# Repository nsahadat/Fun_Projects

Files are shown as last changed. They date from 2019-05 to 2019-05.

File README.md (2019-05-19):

# Fun_Projects
Hobby hardware/software embedded projects:

#### Door_Lock project is built from scratch to control your own door lock using Mobile App via WiFi:
This project includes the following in 4 folders: 
1. PCB design of the board using KiCAD
2. Firmware development of the WiFi module ESP8266
3. Designing the mechanical 3D printed part in Solidworks
4. Android app is developed using MIT App Inventor

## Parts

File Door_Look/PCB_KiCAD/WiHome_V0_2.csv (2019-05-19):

Reference | Value | OrderLink
U2 | LDO_SPX3819 | https://www.digikey.com/scripts/DkSearch/dksus.dll?Detail&itemSeq=225275258&uq=636276384097700233
J1 | ACin | https://www.digikey.com/scripts/DkSearch/dksus.dll?Detail&itemSeq=225275253&uq=636276384097700233
U5 | ESP-12F | http://www.gearbest.com/transmitters-receivers-module/pp_227650.html
D3 | LED | https://www.digikey.com/scripts/DkSearch/dksus.dll?Detail&itemSeq=225275247&uq=636276384097700233
D2 | LED | https://www.digikey.com/scripts/DkSearch/dksus.dll?Detail&itemSeq=225275247&uq=636276384097700233
R7 | 122 | https://www.digikey.com/scripts/DkSearch/dksus.dll?Detail&itemSeq=225275251&uq=636276384097700233
C1 | 10uF | https://www.digikey.com/scripts/DkSearch/dksus.dll?Detail&itemSeq=225275264&uq=636276384097700233
C8 | 0.1uF | https://www.digikey.com/scripts/DkSearch/dksus.dll?Detail&itemSeq=225275262&uq=636276384097700233
C7 | 1uF | https://www.digikey.com/scripts/DkSearch/dksus.dll?Detail&itemSeq=225275264&uq=636276384097700233
J2 | ACout | https://www.digikey.com/scripts/DkSearch/dksus.dll?Detail&itemSeq=225275253&uq=636276384097700233
J3 | FTDI_CON | https://www.digikey.com/scripts/DkSearch/dksus.dll?Detail&itemSeq=225275250&uq=636276384097700233
Q2 | MMBT3904_BEC | https://www.digikey.com/scripts/DkSearch/dksus.dll?Detail&itemSeq=225275260&uq=636276384097700233
R6 | 1k | https://www.digikey.com/scripts/DkSearch/dksus.dll?Detail&itemSeq=225275249&uq=636276384097700233
R5 | 1k | https://www.digikey.com/scripts/DkSearch/dksus.dll?Detail&itemSeq=225275249&uq=636276384097700233
C2 | 0.1uF | https://www.digikey.com/scripts/DkSearch/dksus.dll?Detail&itemSeq=225275262&uq=636276384097700233
C3 | 1uF | https://www.digikey.com/scripts/DkSearch/dksus.dll?Detail&itemSeq=225275264&uq=636276384097700233
C4 | 0.1uF | https://www.digikey.com/scripts/DkSearch/dksus.dll?Detail&itemSeq=225275262&uq=636276384097700233
D1 | D | https://www.digikey.com/scripts/DkSearch/dksus.dll?Detail&itemSeq=225275261&uq=636276384097700233
U3 | AC2DC | http://www.ebay.com/itm/321910440165?_trksid=p2060353.m2749.l2649&ssPageName=STRK%3AMEBIDX%3AIT
U1 | SRD-5VDC | http://www.ebay.com/itm/182396002625?_trksid=p2060353.m2749.l2649&ssPageName=STRK%3AMEBIDX%3AIT
Q1 | MMBT3904_BEC | https://www.digikey.com/scripts/DkSearch/dksus.dll?Detail&itemSeq=225275260&uq=636276384097700233
R3 | 100k | https://www.digikey.com/product-detail/en/yageo/RC0603JR-07100KL/311-100KGRCT-ND/729645
C6 | 0.1uF | https://www.digikey.com/scripts/DkSearch/dksus.dll?Detail&itemSeq=225275262&uq=636276384097700233
R1 | 10k | https://www.digikey.com/product-detail/en/yageo/RC0603JR-0710KL/311-10KGRCT-ND/729647
C5 | 0.1uF | https://www.digikey.com/scripts/DkSearch/dksus.dll?Detail&itemSeq=225275262&uq=636276384097700233
R2 | 10k | https://www.digikey.com/product-detail/en/yageo/RC0603JR-0710KL/311-10KGRCT-ND/729647
U6 | mic | https://www.digikey.com/product-detail/en/cui-inc/CMA-4544PF-W/102-1721-ND/1869981
R4 | 100k | https://www.digikey.com/product-detail/en/yageo/RC0603JR-07100KL/311-100KGRCT-ND/729645
U4 | S | https://www.digikey.com/product-detail/en/cw-industries/GPTS203211B/CW181-ND/3190590

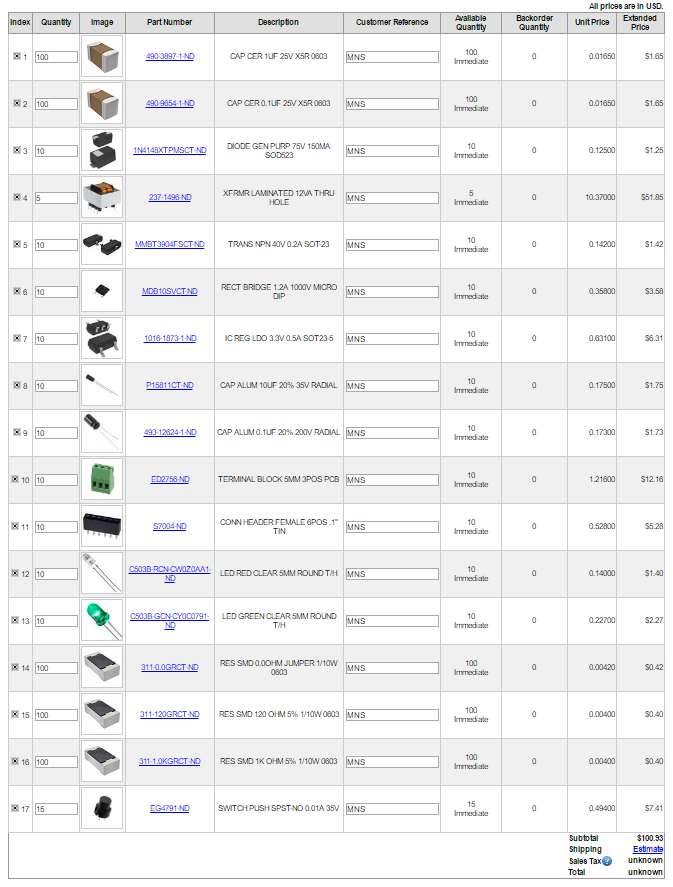
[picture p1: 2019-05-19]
Door_Look/PCB_KiCAD/WiHOME_BOM.PNG

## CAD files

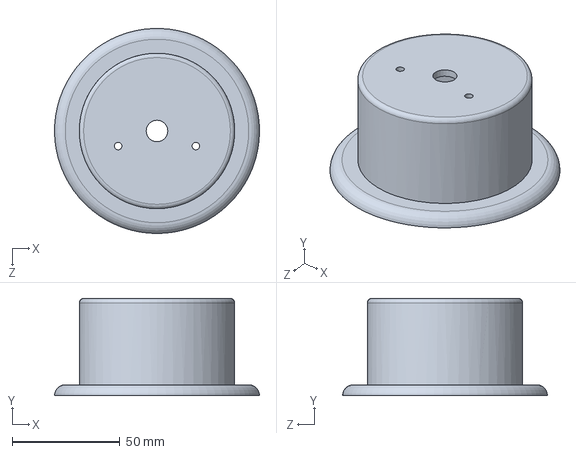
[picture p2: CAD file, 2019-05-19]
Door_Look/Mechanical_Solidwork/Cover.SLDPRT
95.0 x 45.0 x 95.0 mm

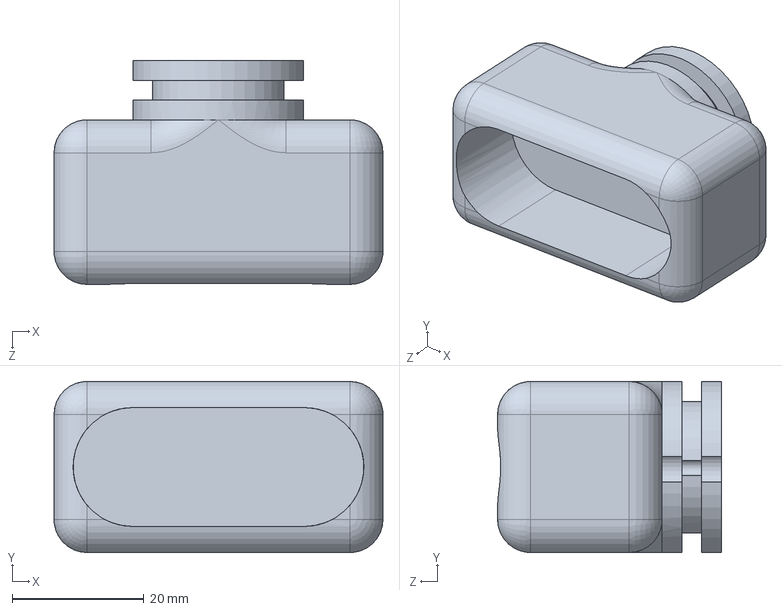
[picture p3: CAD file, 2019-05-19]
Door_Look/Mechanical_Solidwork/pulley_Drive.SLDPRT
50.0 x 26.0 x 34.0 mm

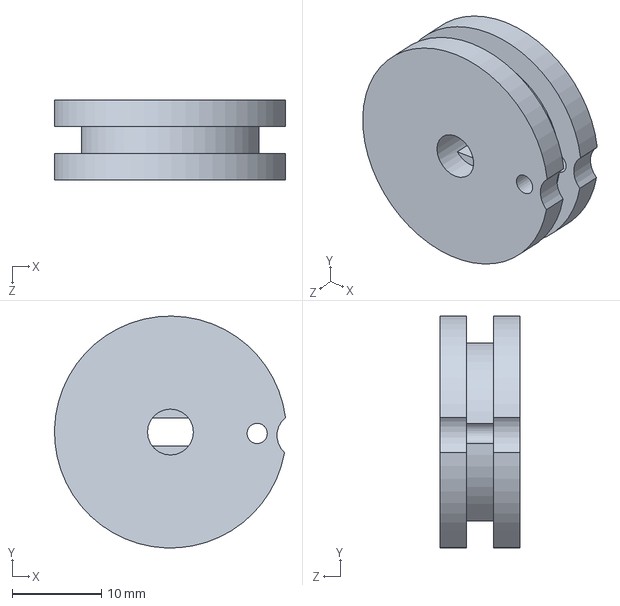
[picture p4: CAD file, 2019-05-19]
Door_Look/Mechanical_Solidwork/pulley.SLDPRT
25.9 x 26.0 x 9.00 mm

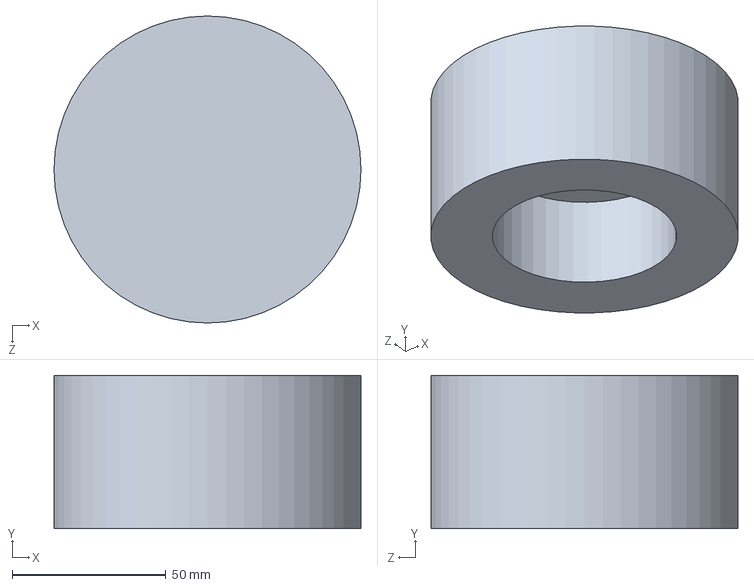
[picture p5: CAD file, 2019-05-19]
Door_Look/Mechanical_Solidwork/DoorLock.SLDPRT
100.0 x 50.0 x 100.0 mm

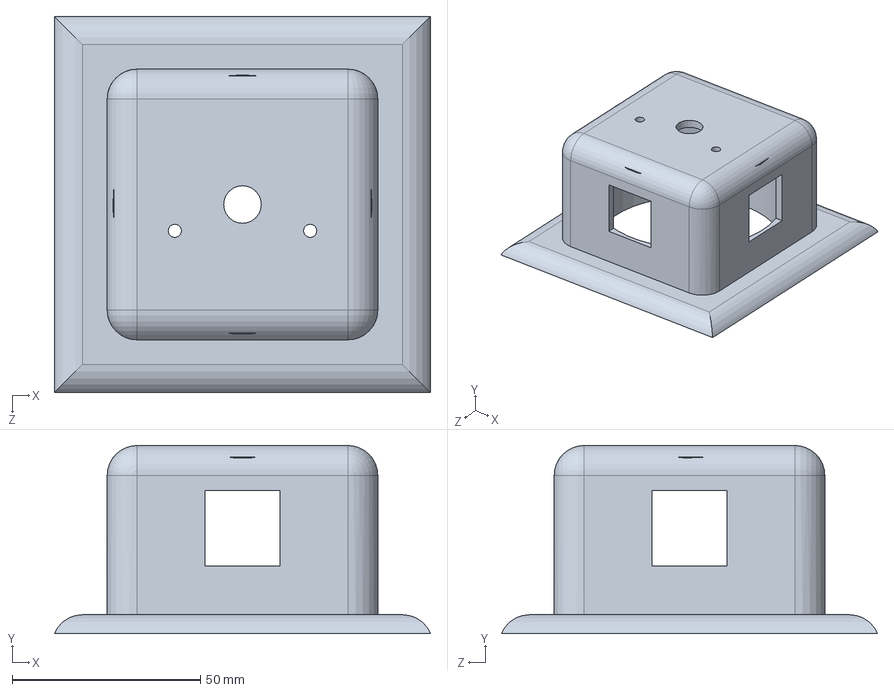
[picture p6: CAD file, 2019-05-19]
Door_Look/Mechanical_Solidwork/Cover_V2.SLDPRT
100.0 x 50.0 x 100.0 mm

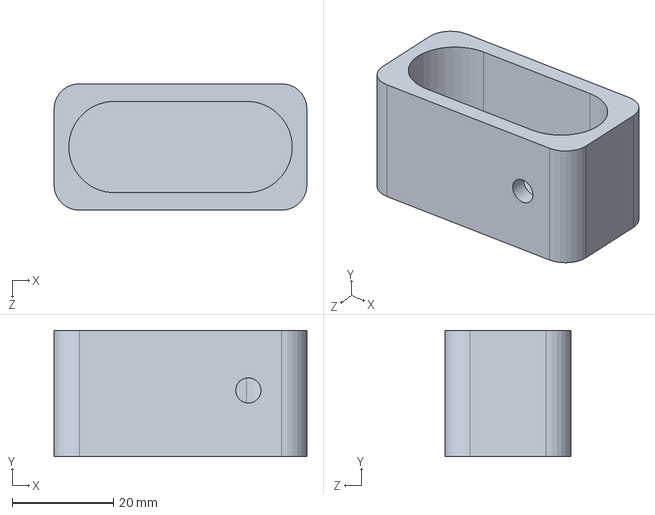
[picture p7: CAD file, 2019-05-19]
Door_Look/Mechanical_Solidwork/DoorLock_P1.SLDPRT
50.0 x 25.0 x 25.0 mm

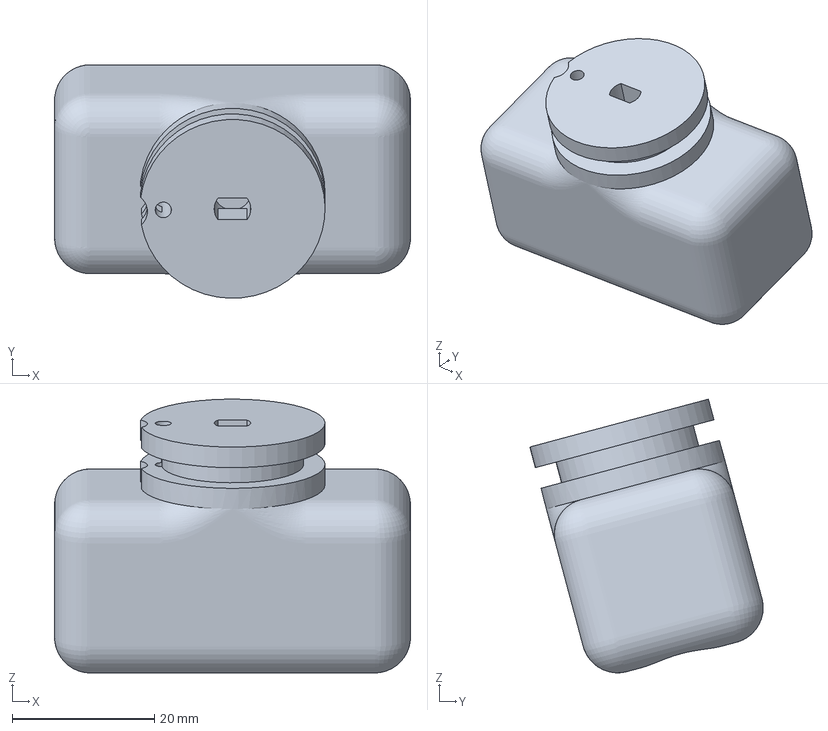
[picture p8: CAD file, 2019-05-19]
Door_Look/Mechanical_Solidwork/PI3_pulley_Drive.curaproject.3mf
50.0 x 32.8 x 38.4 mm

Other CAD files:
Door_Look/Mechanical_Solidwork/Cover.STL
Door_Look/Mechanical_Solidwork/pulley.STL
Door_Look/Mechanical_Solidwork/pulley_Drive.STL

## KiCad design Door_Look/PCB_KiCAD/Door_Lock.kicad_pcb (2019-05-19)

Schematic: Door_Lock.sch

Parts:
C1, C11: 10uF; C_0603
C2, C5, C6, C8: 0.1uF; C_0603
C3, C7, C9: 1uF; C_0603
C4, C13: 10nF; C_0603
C10, C12, C14: 100nF; C_0603
D3: LED; LED-5MM
J3: FTDI_CON; CON6
P1: USB_OTG; USB_Micro-B_Molex_47346-0001
Q1: MMBT3904_BEC; MMBT3904
R1: 200k; R_0603
R2: 1k; R_0603
R3, R4: 100k; R_0603
R5: 0; R_0603
R7: 122; R_0603
U1: push_button; push_switch
U2: LDO_SPX3819; SPX3819
U3: motor_con; motor_conn
U4: ULN2003A; ULN2003a
U5: ESP-12F; ESP12F
U6: mic
U7: LSM9DS1

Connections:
+3V3: C3.1, C7.1, C8.1, C10.1, C11.1, C14.1, J3.4 (VCC), R1.2, R2.2, R4.2, R5.2, U2.5 (Vout), U5.3 (EN), U5.8 (VCC), U7.1 (VDD_IO), U7.3 (VDD_IO), U7.22 (VDD), U7.23 (VDD)
+5V: C1.1, C2.1, C9.1, P1.1, U2.1 (VIN), U2.3 (EN), U3.5 (VCC), U4.9
/CS_A_G: U5.12 (IO10), U7.7 (CS_A/G)
/CS_M: U5.11 (IO09), U7.8 (CS_M)
/IN1: U4.1, U5.7 (IO13)
/IN2: U4.2, U5.6 (IO12)
/IN3: U4.3, U5.5 (IO14)
/IN4: U4.4, U5.4 (IO16)
/MISO: U5.10 (MISO), U7.5 (SDO_A/G), U7.6 (SDO_M)
/MOSI: U5.13 (MOSI), U7.4 (SDA/SDI/SDO)
/SCK: U5.14 (SCLK), U7.2 (SCL/SPC)
GND: C1.2, C2.2, C3.2, C4.2, C7.2, C8.2, C9.2, C10.2, C11.2, C12.2, C13.1, C14.2, J3.6 (GND), P1.5, P1.6, Q1.2 (E), R7.2, U1.1, U2.2 (GND), U4.8, U5.15 (GND), U5.16 (IO15), U6.2 (-), U7.14 (RES), U7.15 (RES), U7.16 (RES), U7.17 (RES), U7.18 (RES), U7.19 (GND), U7.20 (GND)
unnamed: C4.1, U2.4 (BP)
unnamed: C5.1, U5.2 (ADC)
unnamed: C5.2, Q1.3 (C), R1.1, R3.1
unnamed: C6.1, Q1.1 (B), R3.2
unnamed: C6.2, R2.1, U6.1 (+)
unnamed: C12.1, U7.24 (C1)
unnamed: C13.2, U7.21 (CAP)
unnamed: D3.1 (K), R7.1
unnamed: D3.2 (A), U5.17 (IO02)
unnamed: J3.2 (RX), U5.22 (TXD)
unnamed: J3.3 (TX), U5.21 (RXD)
unnamed: R4.1, U1.3, U5.18 (IO00)
unnamed: R5.1, U7.13 (DEN_A/G)
unnamed: U3.1 (IN1), U4.16
unnamed: U3.2 (IN2), U4.15
unnamed: U3.3 (IN3), U4.14
unnamed: U3.4 (IN4), U4.13

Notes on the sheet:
April 11th, 2017
Wi Home Project
Version: 0.2
POWER SUPPLY AC-->DC (5V) --> 3.3V SUPPLY
WiFi MODULE & RELAY INTERFACE, BUTTONS & INDICATORS
IMU: LSM9DS1

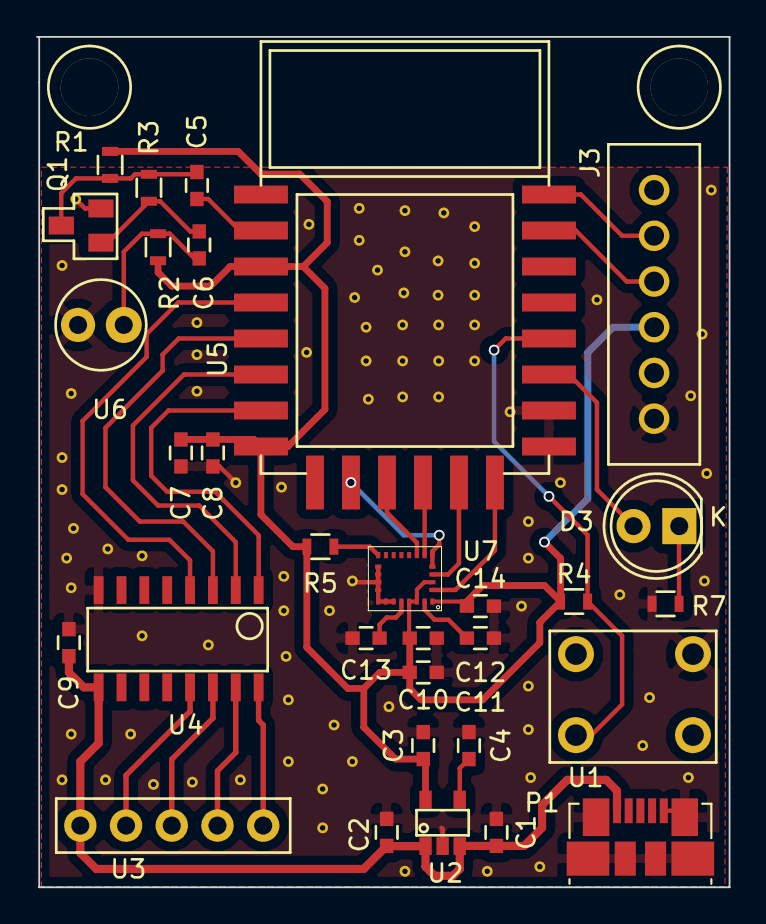
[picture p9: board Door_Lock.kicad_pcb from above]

Board: 2 copper layers, 38.5 x 47.2 mm, 31 parts (0 on the bottom side), 29 nets.

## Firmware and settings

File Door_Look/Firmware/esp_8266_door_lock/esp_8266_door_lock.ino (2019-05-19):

#include <ESP8266WiFi.h>
#include <ESP8266mDNS.h>
#include <ESP8266WebServer.h>
#include <ESP8266SSDP.h>
#include <WiFiUdp.h>
#include <ArduinoOTA.h>
#include <StepperMotor.h>


//-------------all the defines---------------------------//
#define WIFI_SSID "****"
#define WIFI_PASS "****"


#define led 2
#define button 0
// define the motor input

#define In1 13
#define In2 12
#define In3 14
#define In4 16


//---------------global variables--------------------------------//
int ledState = LOW;          // the current state of the output pin
int buttonState;             // the current reading from the input pin
int doorstep = 1200;
int lastButtonState = LOW;   // the previous reading from the input pin
int resetState = HIGH;

// the following variables are unsigned long's because the time, measured in miliseconds,
// will quickly become a bigger number than can be stored in an int.
unsigned long lastDebounceTime = 0;  // the last time the output pin was toggled
unsigned long debounceDelay = 100;   // the debounce time; increase if the output flickersy
unsigned long resetDelay = 3000;     // how long (milisec) to hold the reset button to restart


// static ip setup
IPAddress ip(192, 168, 0, 111); // where xx is the desired IP Address
IPAddress gateway(192, 168, 0, 1); // set gateway to match your network

IPAddress subnet(255, 255, 255, 0); // set subnet mask to match your network

//----------------global objects-------------------------------//
ESP8266WebServer HTTP(80);
StepperMotor motor(In1, In2, In3, In4);


//----------------local function definitions----------------------------//

void pinmap(void);

//----------------functions---------------------------------//
void setup()
{
  Serial.begin(115200);
  pinmap();
  motor.setStepDuration(1);   // motor step duration

  Serial.println("Starting WiFi...");
  WiFi.config(ip, gateway, subnet);
  WiFi.mode(WIFI_STA);
  WiFi.begin(WIFI_SSID, WIFI_PASS);
  while (WiFi.waitForConnectResult() != WL_CONNECTED)
  {
    Serial.println("Connection Failed! Rebooting...");
    delay(5000);
    ESP.restart();
  }
  digitalWrite(led, LOW);

  //Serial.printf("Starting HTTP...\n");
  HTTP.on("/H", HTTP_GET, []()
  {
    motor.step(-1200);
    delay(2000);

    digitalWrite(led, HIGH);
    HTTP.send(200, "application/json", "Door Opened");

    // turn the motor controller to power down mode
    digitalWrite(In1, LOW);
    digitalWrite(In2, LOW);
    digitalWrite(In3, LOW);
    digitalWrite(In4, LOW);
  });

  HTTP.on("/L", HTTP_GET, []()
  {
    motor.step(1200);
    delay(2000);

    digitalWrite(led, LOW);
    HTTP.send(200, "application/json", "Door Closed");

    // turn the motor controller to power down mode
    digitalWrite(In1, LOW);
    digitalWrite(In2, LOW);
    digitalWrite(In3, LOW);
    digitalWrite(In4, LOW);

  });

  HTTP.on("/S", HTTP_GET, []()
  {
    int val = digitalRead(led);
    if (val == 1) {
      HTTP.send(200, "application/json", "Door Opened");
    } else {
      HTTP.send(200, "application/json", "Door closed");
    }
  });

  HTTP.on("/description.xml", HTTP_GET, []()
  {
    SSDP.schema(HTTP.client());
  });

  HTTP.begin();
  blinkLed(3);
}

void loop()
{

  HTTP.handleClient();

  // read the state of the switch into a local variable:
  int reading = digitalRead(button);

  // check to see if you just pressed the button
  // (i.e. the input went from LOW to HIGH),  and you've waited
  // long enough since the last press to ignore any noise:

  // If the switch changed, due to noise or pressing:
  if (reading != lastButtonState)
  {
    // reset the debouncing timer
    lastDebounceTime = millis();
  }

  if ((millis() - lastDebounceTime) > resetDelay)
  {
    if (reading != resetState)
    {
      resetState = reading;

      if (resetState == LOW)
      {
        blinkLed(4);
        //Serial.printf("Resetting...\n\r");
        ESP.restart();
      }
    }
  }
  else
  {
    if ((millis() - lastDebounceTime) > debounceDelay)
    {
      // whatever the reading is at, it's been there for longer
      // than the debounce delay, so take it as the actual current state:

      // if the button state has changed:
      if (reading != buttonState)
      {
        buttonState = reading;

        // only toggle the LED if the new button state is HIGH
        if (buttonState == HIGH)
        {
          ledState = !ledState;
          doorstep = -doorstep;
          digitalWrite(led, ledState);

          motor.step(doorstep);
          delay(2000);

          // turn the motor controller to power down mode
          digitalWrite(In1, LOW);
          digitalWrite(In2, LOW);
          digitalWrite(In3, LOW);
          digitalWrite(In4, LOW);


        }

      }
    }
  }

  lastButtonState = reading;
  delay(1);

  //sound = analogRead(A0);     // read sound
  //Serial.printf("%d\n",sound);  // display sound
}

void blinkLed(int times)
{
  while (times > 0)
  {
    digitalWrite(led, LOW);
    delay(300);
    digitalWrite(led, HIGH);
    delay(300);
    times--;
  }
}

void pinmap(void)
{
  pinMode(led, OUTPUT);    //Green LED (reverse)
  pinMode(button, INPUT);  //Button
  // motor control pin mode change to output
  pinMode(In1, OUTPUT);
  pinMode(In2, OUTPUT);
  pinMode(In3, OUTPUT);
  pinMode(In4, OUTPUT);

}
